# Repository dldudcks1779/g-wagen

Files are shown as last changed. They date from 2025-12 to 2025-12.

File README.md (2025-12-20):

# 떡상한 구독자 수! 바로 G바겐 뽑았습니다
<div align="center">
  <a href="https://www.youtube.com/watch?v=YYdsRcfBJVY">
    YouTube
  </a>
</div>

---

## 1. System Architecture
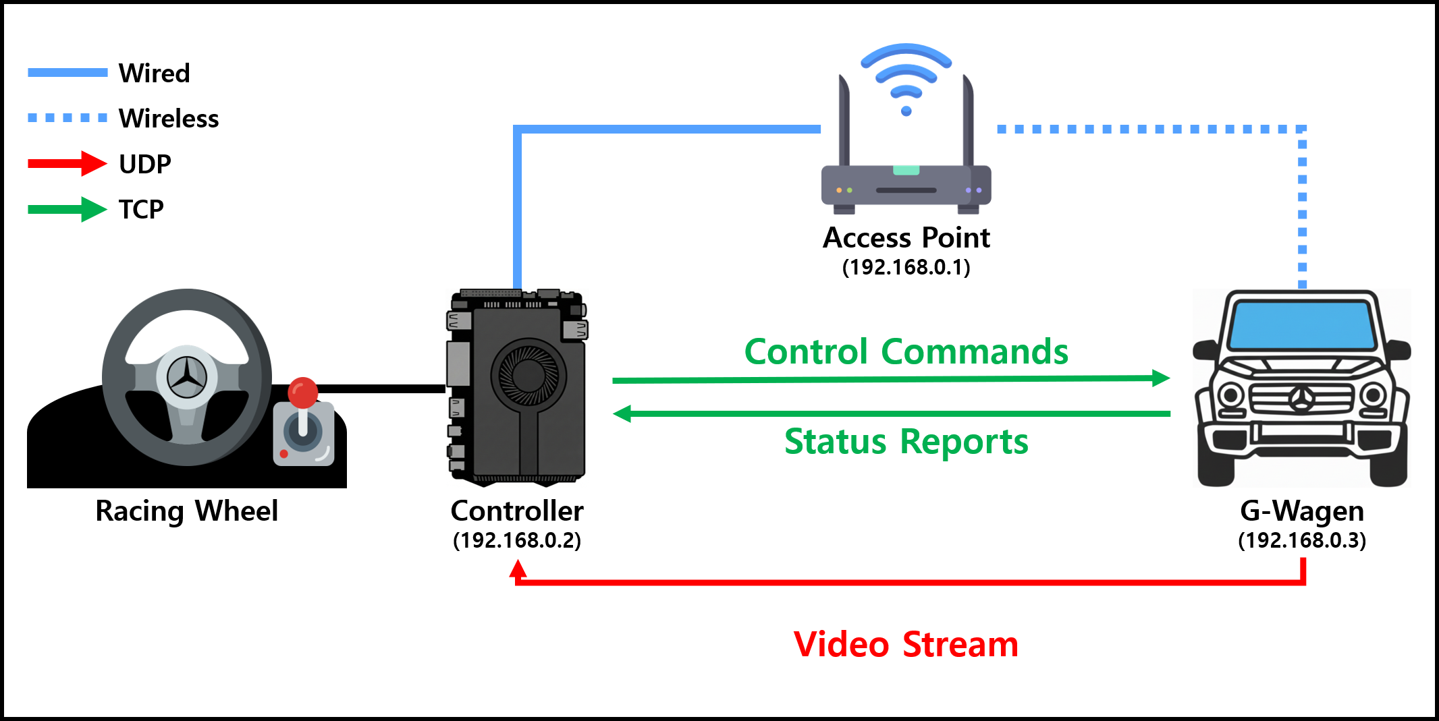
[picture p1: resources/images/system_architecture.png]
System Architecture


- **Video Stream**
    - **Protocol:** UDP
        - **Port:** 5000
    - **Codec:** MJPEG
    - **Resolution:** 1920x1080
    - **Frame Rate:** 15 fps
    - **Format:** Inline
- **Control Commands**
    - **Protocol:** TCP
        - **Port:** 5001
    - **Payload:** Steering Value, Steering Direction, Acceleration Percent, Brake Percent, Gear, Headlight, Hazard Light, Horn
- **Status Reports**
    - **Protocol:** TCP
        - **Port:** 5001
    - **Payload:** Battery SoC (State of Charge)
- **Access Point** 
    - **SSID (Service Set ID):** `Mercedes-Benz`
    - **PSK (Pre-Shared Key):** `20220608`

---

## 2. Hardware Information
### 2.1) G-Wagen
- **Main Board:** Raspberry Pi Zero 2 W
    - **Processor:** Broadcom BCM2710A1, quad-core 64-bit SoC (Arm Cortex-A53 @ 1GHz)
    - **Memory:** 512MB LPDDR2
    - **Storage:** 16GB microSD Card
    - **[Product Brief](./resources/[Raspberry%20Pi%20Zero%202%20W]%20Product%20Brief.pdf)**
- **Camera:** Raspberry Pi Camera Module V2 (8MP)
- **Motor Driver:** L9110S Dual H-Bridge
- **Speaker:** LM386 Audio Amplifier
- **Battery**
    - **Capacity:** 5000mAh (3.7V)
    - **Fuel Gauge:** Gravity 3.7V Li Battery Fuel Gauge SKU DFR0563
        - **Link:** [https://wiki.dfrobot.com/gravity__3.7v_li_battery_fuel_gauge_sku__dfr0563](https://wiki.dfrobot.com/gravity__3.7v_li_battery_fuel_gauge_sku__dfr0563)
    - **Management IC:** IP5306 (Li-ion Charge/Boost Controller)
- **Circuit Diagram**<br>
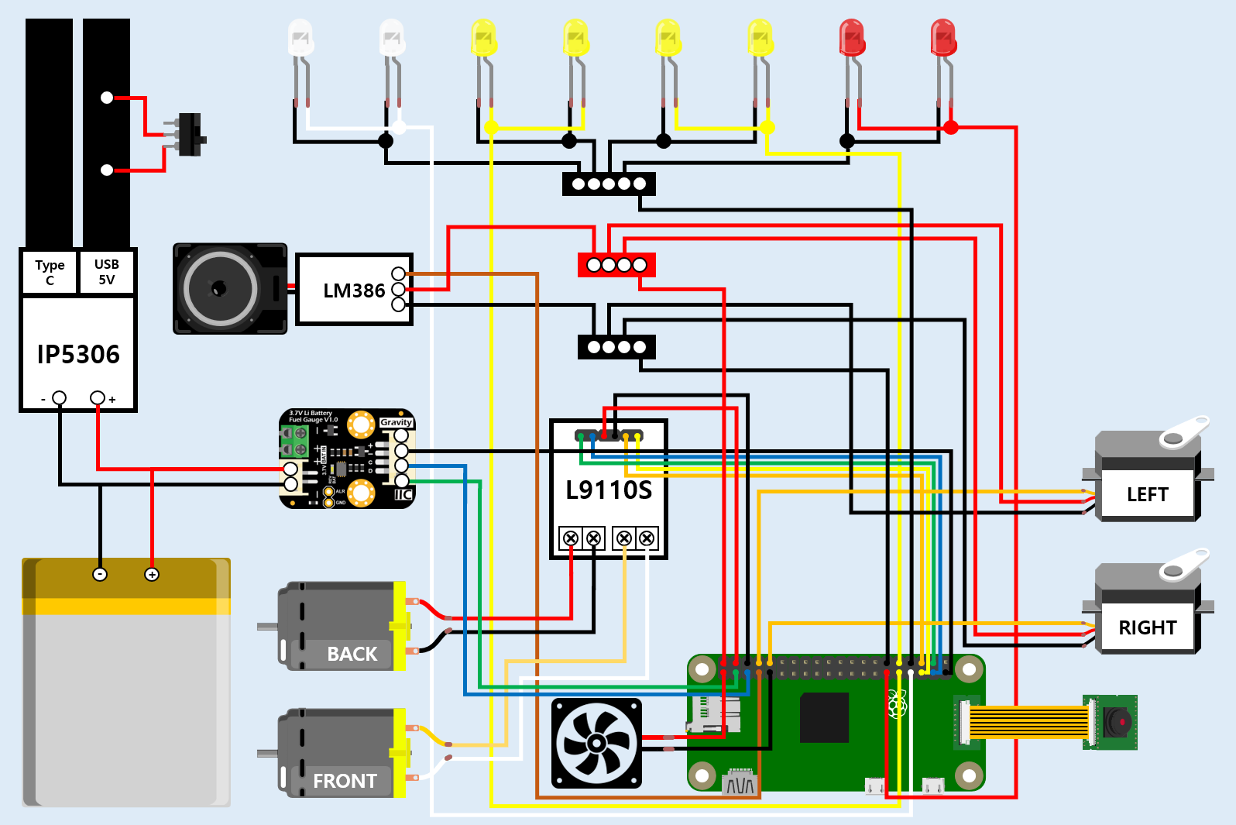
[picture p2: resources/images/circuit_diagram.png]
Circuit Diagram
    
### 2.2) Controller
- **Main Board:** LattePanda Sigma
    - **Processor:** Intel Core i5-1340P 12 Cores, 16 Threads Up to 4.6GHz
    - **Graphics:** Intel Iris Xe Graphics 80 Execution Units Up to 1.45GHz
    - **Memory:** 16GB Dual Channels LPDDR5 6400MHz
    - **Storage:** 512GB NVMe SSD
    - **Specification:** [https://docs.lattepanda.com/content/sigma_edition/Specification/](https://docs.lattepanda.com/content/sigma_edition/Specification/)
- **Racing Wheel:** [POWER RACER 270R REVOLUTION](./resources/[POWER%20RACER%20270R%20REVOLUTION]%20manual.pdf)

---

## 3. Software Information
### 3.1) G-Wagen
- **Operating System:** Raspberry Pi OS with Desktop (64-bit)
    - **Debian Codename:** Bookworm (Version 12)
    - **Download Link:** [https://downloads.raspberrypi.org/raspios_arm64/images/raspios_arm64-2025-05-13/](https://downloads.raspberrypi.org/raspios_arm64/images/raspios_arm64-2025-05-13/)
- **Language & Libraries**
    - 
        - 
- **Account Information**
    - **username:** `gwagen`
    - **password:** `0608`
### 3.2) Controller
- **Operating System:** Ubuntu with Desktop (64-bit)
    - **Debian Codename:** Noble Numbat (Version 24.04.3 LTS)
    - **Download Link:** [https://releases.ubuntu.com/noble/](https://releases.ubuntu.com/noble/)
- **Language & Libraries**
    - 
        -  
- **Account Information**
    - **username:** `controller`
    - **password:** `0608`

---

## 4. Setup Instructions
### 4.1) G-Wagen
#### 4.1.1) Raspberry Pi Configuration
- **Interfaces**    
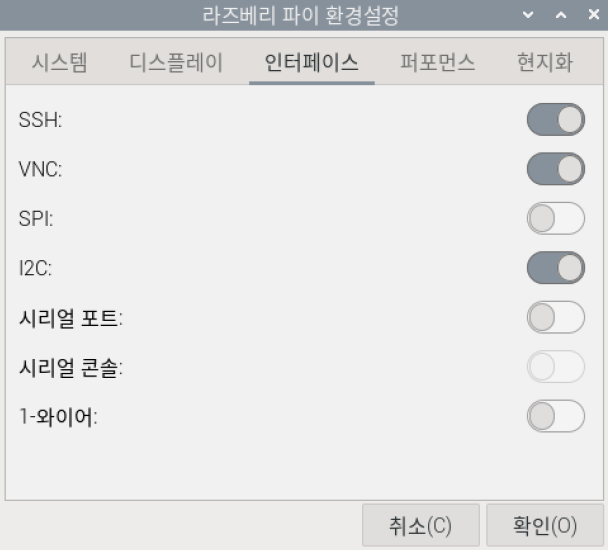
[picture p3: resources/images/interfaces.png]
    
    - **SSH (Secure Shell) Enabled**
    - **VNC (Virtual Network Computing) Enabled**
    - **I2C (Inter-Integrated Circuit) Enabled**
#### 4.1.2) System Update
- **Update Package List**
    ```bash
    sudo apt update
    ```
- **Upgrade Installed Packages**
    ```bash
    sudo apt upgrade -y
    ```
#### 4.1.3) Install Libraries
##### 4.1.3.1) System Dependencies and Core Packages (APT)
- **Install Required Packages**
    ```bash
    sudo apt install -y pigpio
    ```
    - **pigpio:** C library for Raspberry Pi which allows control of the General Purpose Input Outputs (GPIO)
##### 4.1.3.2) Specific Python Modules (pip3)
- **Install Required Python Modules**
    ```bash
    sudo pip3 install smbus2==0.5.0 --break-system-packages
    ```
    - **smbus2:** Pure Python implementation for I2C protocol communication
        - `--break-system-packages`: Allows installation of packages that may conflict with system packages
#### 4.1.4) Enable pigpio Daemon
- **Enable and Start pigpiod Service**
    ```bash
    sudo systemctl enable --now pigpiod
    ```
    - **systemctl:** Command to examine and control the systemd system and service manager
        - `--now`: Start the service immediately
### 4.2) Controller
#### 4.2.1) System Update
- **Update Package List**
    ```bash
    sudo apt update
    ```
- **Upgrade Installed Packages**
    ```bash
    sudo apt upgrade -y
    ```
#### 4.2.2) Install Libraries
##### 4.2.2.1) System Dependencies and Core Packages (APT)
- **Install Required Packages**
    ```bash
    sudo apt install -y python3-pip python3-opencv python3-pygame
    ```
    - **python3-pip:** Package installer for Python 3
    - **python3-opencv:** Library of programming functions primarily for real-time computer vision tasks
    - **python3-pygame:** Set of Python modules designed for writing video games
##### 4.2.2.2) Specific Python Modules (pip3)
- **Install Required Python Modules**
    ```bash
    sudo pip3 install pyinstaller --break-system-packages
    ```
    - **pyinstaller:** Tool to bundle Python applications into standalone executables
        - `--break-system-packages`: Allows installation of packages that may conflict with system packages

---

## 5. Start Video Stream on G-Wagen
- **Run rpicam-vid Command**
    ```bash
    rpicam-vid -t 0 --width 1920 --height 1080 --framerate 15 --codec mjpeg --inline --nopreview -o udp://192.168.0.2:5000
    ```
    - **rpicam-vid:** Command-line tool for streaming video from the Raspberry Pi Camera Module
        - `-t:` Duration of the video stream
        - `--width:` Width of the video frame
        - `--height:` Height of the video frame
        - `--framerate:` Frames per second
        - `--codec:` Video codec to use
        - `--inline:` Embed JPEG frames directly in the stream
        - `--nopreview:` Disable preview window
        - `-o:` Output destination

---

## 6. Auto-start G-Wagen Services on Boot
### 6.1) Create RPi Camera Video Stream Service
- **Open the file using a text editor**
    ```bash
    sudo vi /etc/systemd/system/rpicam.service
    ```
    - **Add the following content**
        ```ini
        [Unit]
        Description=RPi Camera Video Stream
        Wants=network-online.target
        After=network-online.target
        
        [Service]
        User=gwagen
        Group=gwagen
        Type=simple
        WorkingDirectory=/home/gwagen
        ExecStart=/usr/bin/rpicam-vid -t 0 --width 1920 --height 1080 --framerate 15 --codec mjpeg --inline --nopreview -o udp://192.168.0.2:5000
        Restart=on-failure
        RestartSec=5

        [Install]
        WantedBy=multi-user.target
        ```
        - **[Unit] Section**
            - `Description`: Brief description of the service
            - `Wants`: Specifies the target that this service wants to be started with
            - `After`: Specifies the order in which units are started
        - **[Service] Section**
            - `User`: User to run the service as
            - `Group`: Group to run the service as
            - `Type`: Specifies the process start-up type
            - `WorkingDirectory`: Directory where the service will run
            - `ExecStart`: Command to start the service
            - `Restart`: Defines the restart behavior on failure
            - `RestartSec`: Delay before restarting the service
        - **[Install] Section**
            - `WantedBy`: Specifies the target that this service should be started under
### 6.2) Create G-Wagen Application Service
- **Open the file using a text editor**
    ```bash
    sudo vi /etc/systemd/system/gwagen.service
    ```
    - **Add the following content**
        ```ini
        [Unit]
        Description=G-Wagen Application
        Wants=network-online.target
        After=network-online.target
        After=rpicam.service
        
        [Service]
        User=gwagen
        Group=gwagen
        Type=simple
        WorkingDirectory=/home/gwagen
        ExecStart=/usr/bin/python3 /home/gwagen/main.py
        Restart=on-failure
        RestartSec=5

        [Install]
        WantedBy=multi-user.target
        ```
        - **[Unit] Section**
            - `Description`: Brief description of the service
            - `Wants`: Specifies the target that this service wants to be started with
            - `After`: Specifies the order in which units are started
        - **[Service] Section**
            - `User`: User to run the service as
            - `Group`: Group to run the service as
            - `Type`: Specifies the process start-up type
            - `WorkingDirectory`: Directory where the service will run
            - `ExecStart`: Command to start the service
            - `Restart`: Defines the restart behavior on failure
            - `RestartSec`: Delay before restarting the service
        - **[Install] Section**
            - `WantedBy`: Specifies the target that this service should be started under
### 6.3) Enable Both Services
- **Reload Systemd Daemon**
    ```bash
    sudo systemctl daemon-reload
    ```
- **Enable both services to start on boot**
    ```bash
    sudo systemctl enable rpicam.service gwagen.service
    ```
- **Start both services immediately**
    ```bash
    sudo systemctl start rpicam.service gwagen.service
    ```
- **Check the status of both services**
    ```bash
    sudo systemctl status rpicam.service gwagen.service
    ```
### 6.4) Apply Changes
- **Apply Changes by Rebooting**
    ```bash
    sudo reboot
    ```

---

## 7. Build Controller Application Executable
- **Use PyInstaller to Create Executable**
    ```bash
    pyinstaller --onedir --noconsole --name controller main.py
    ```
    - **pyinstaller:** Tool to bundle Python applications into standalone executables
        - `--onedir:` Create a directory with the executable and dependencies
        - `--noconsole:` Do not provide a console window for standard i/o
        - `--name:` Specify the name of the executable file

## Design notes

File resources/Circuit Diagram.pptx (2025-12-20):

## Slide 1

Type
C

USB 5V

LM386

IP5306

+

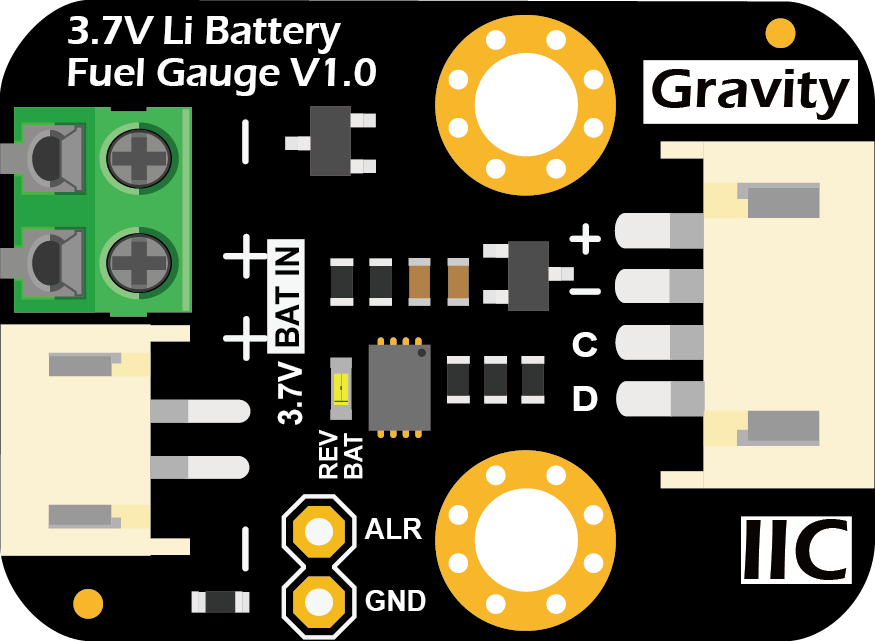
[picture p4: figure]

L9110S

LEFT

RIGHT

+

BACK

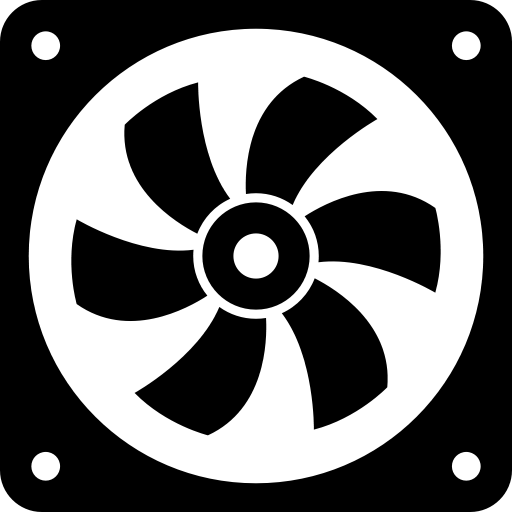
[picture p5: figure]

FRONT

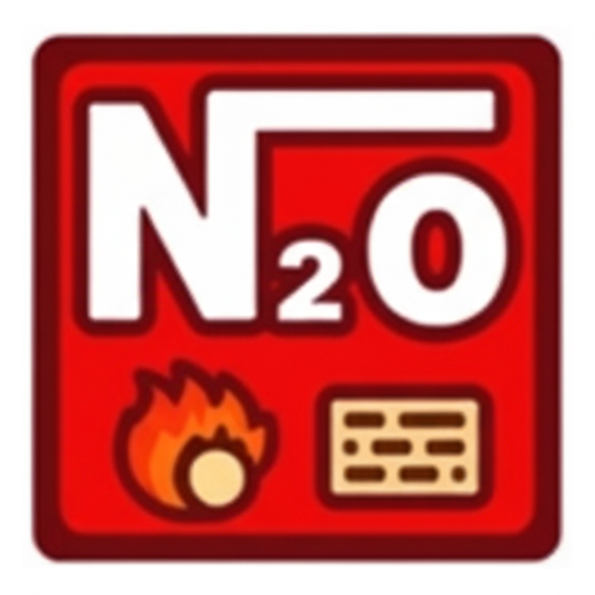
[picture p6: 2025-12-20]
controller/images/battery.png

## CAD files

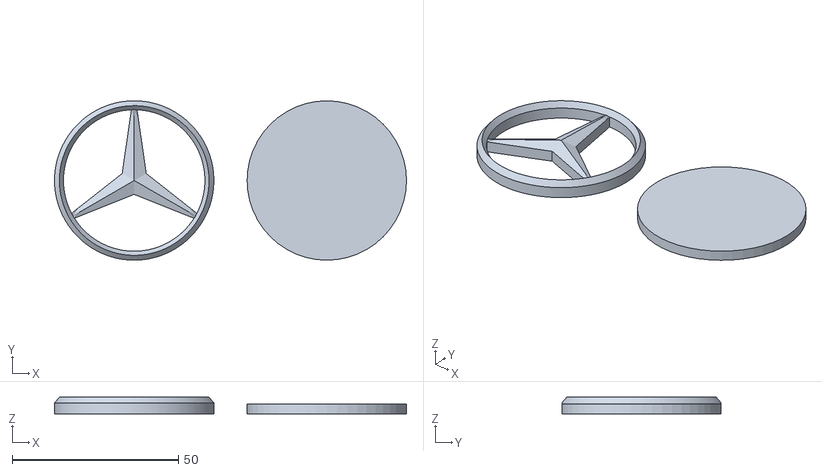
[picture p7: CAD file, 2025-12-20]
resources/3d/mercedes_benz_logo.stl
106.0 x 48.0 x 5.00

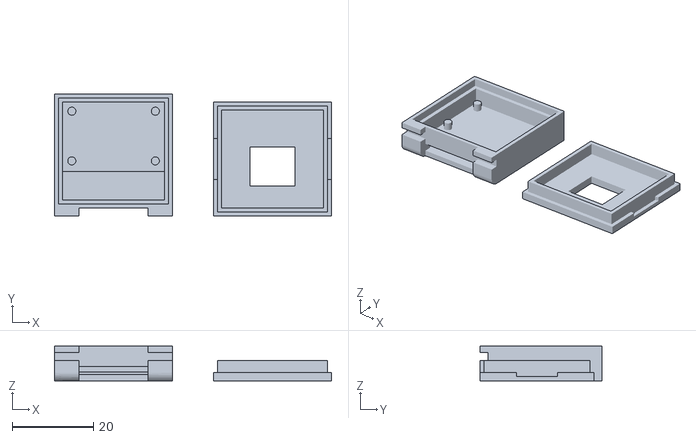
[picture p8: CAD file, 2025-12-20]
resources/3d/raspberry_pi_camera_case.stl
68.0 x 30.0 x 8.50

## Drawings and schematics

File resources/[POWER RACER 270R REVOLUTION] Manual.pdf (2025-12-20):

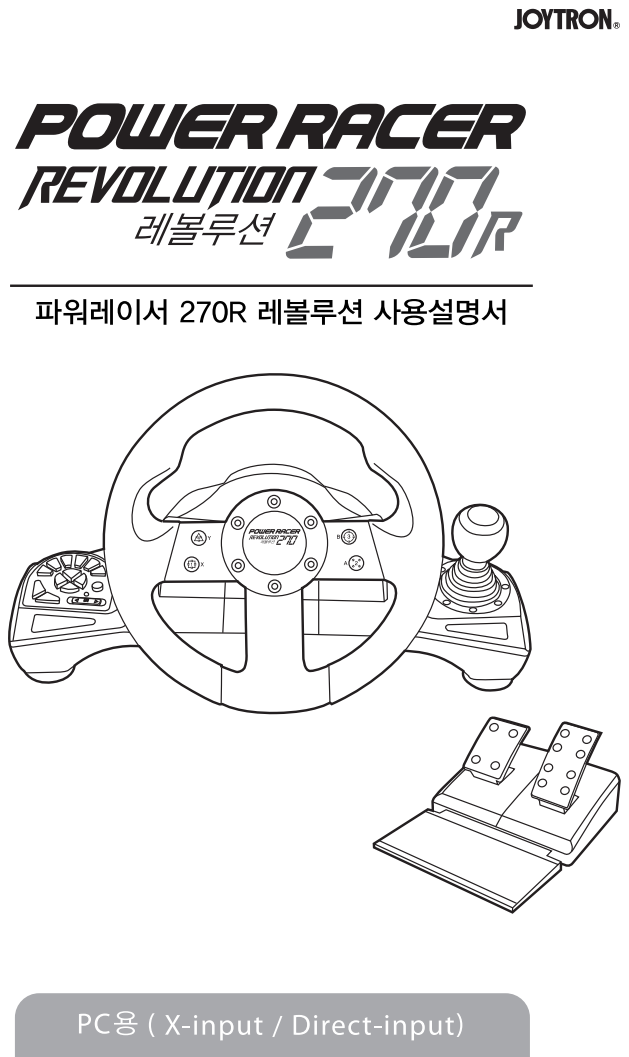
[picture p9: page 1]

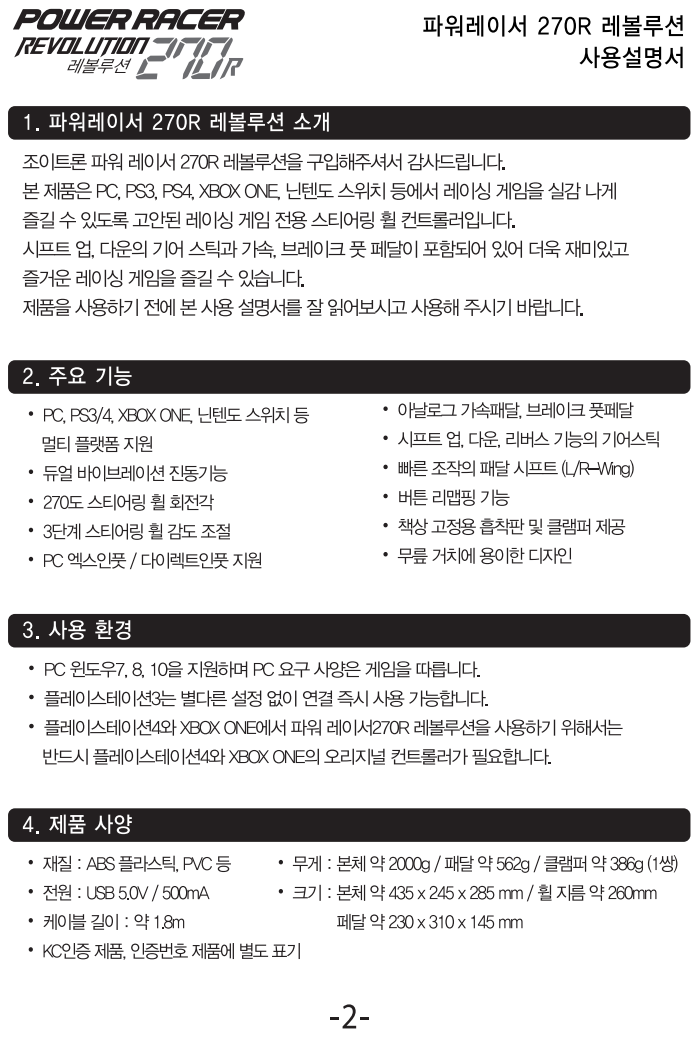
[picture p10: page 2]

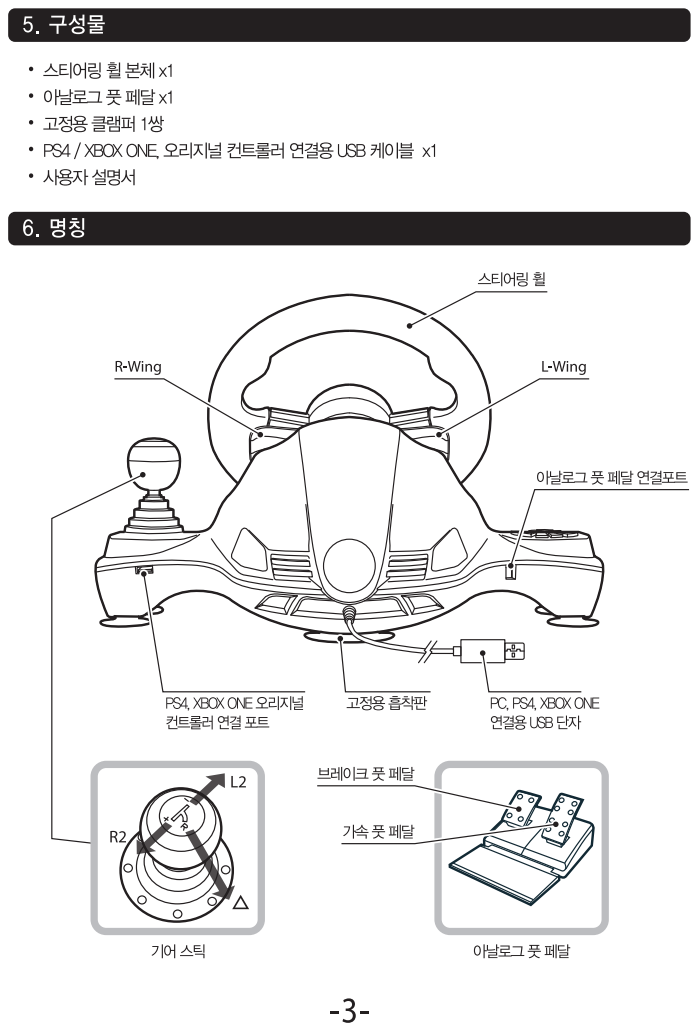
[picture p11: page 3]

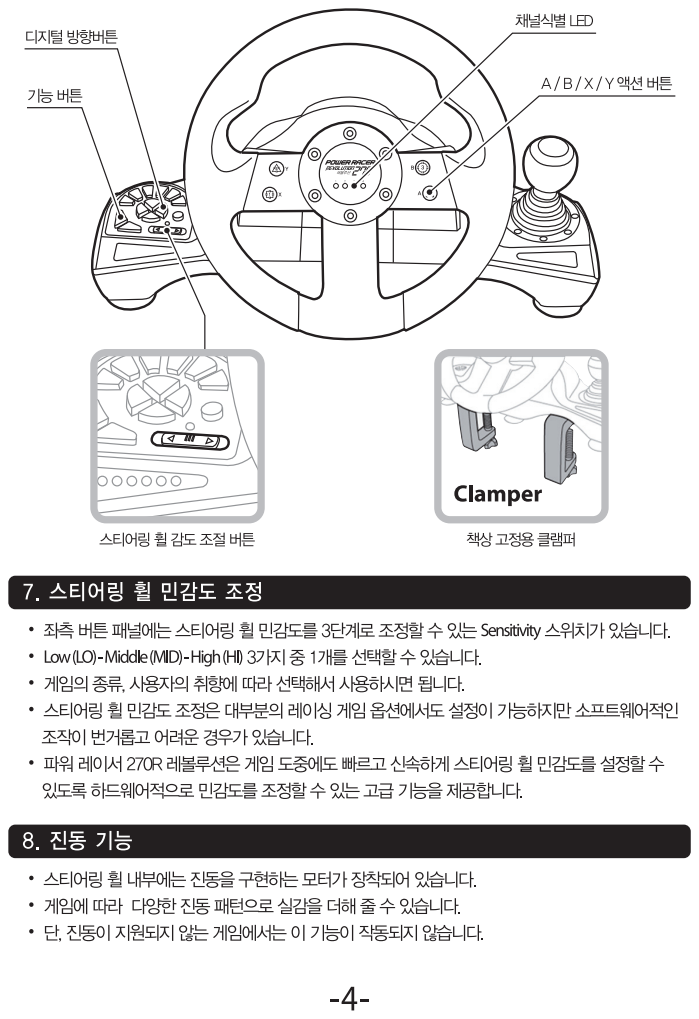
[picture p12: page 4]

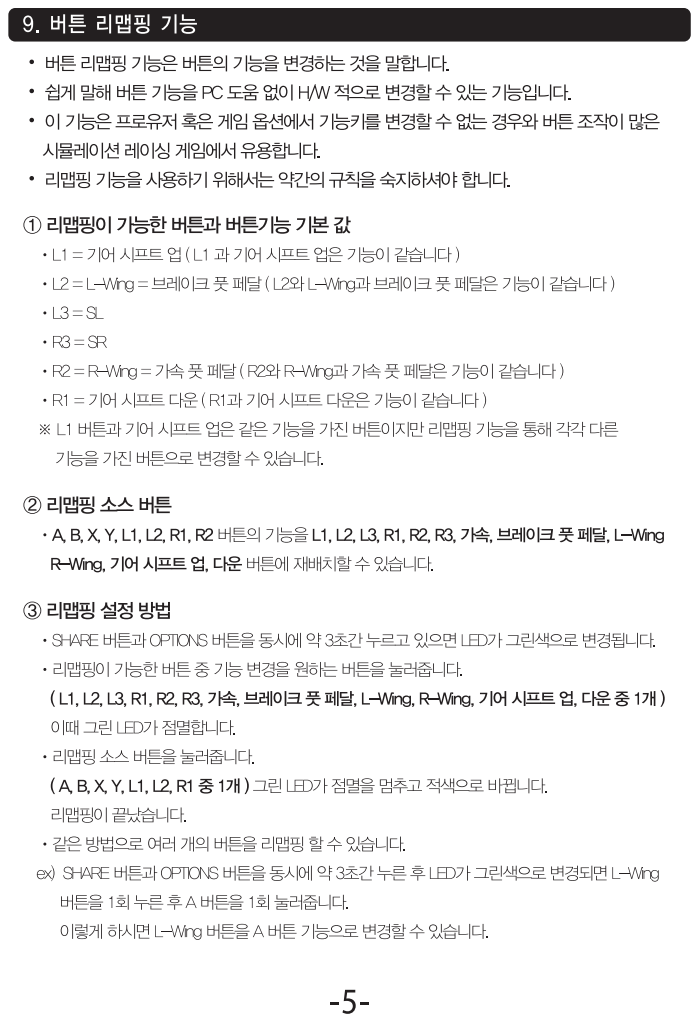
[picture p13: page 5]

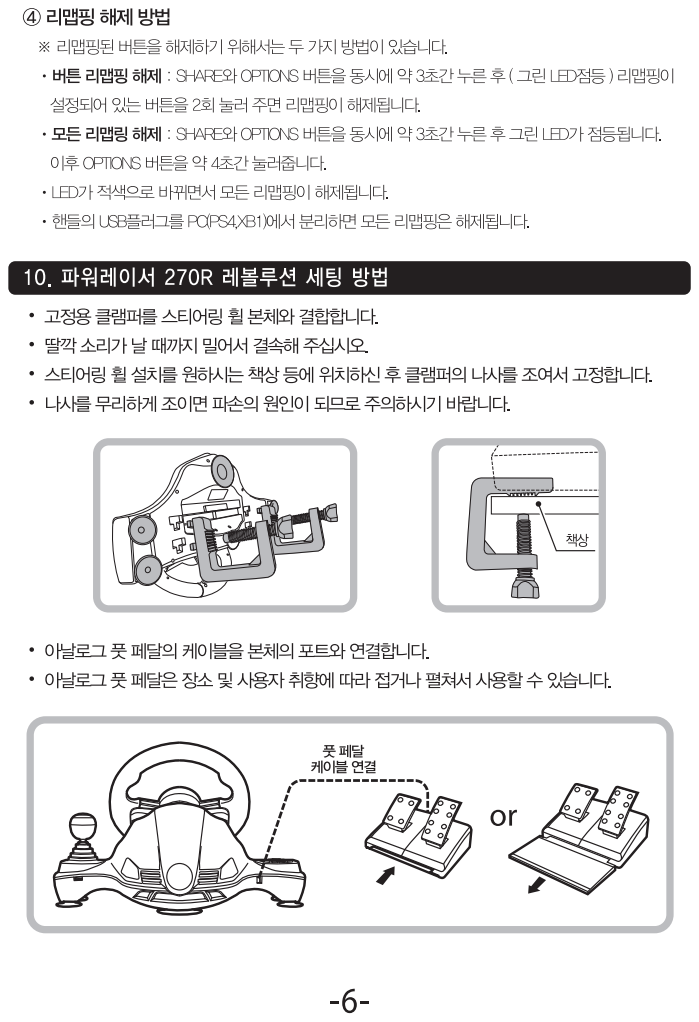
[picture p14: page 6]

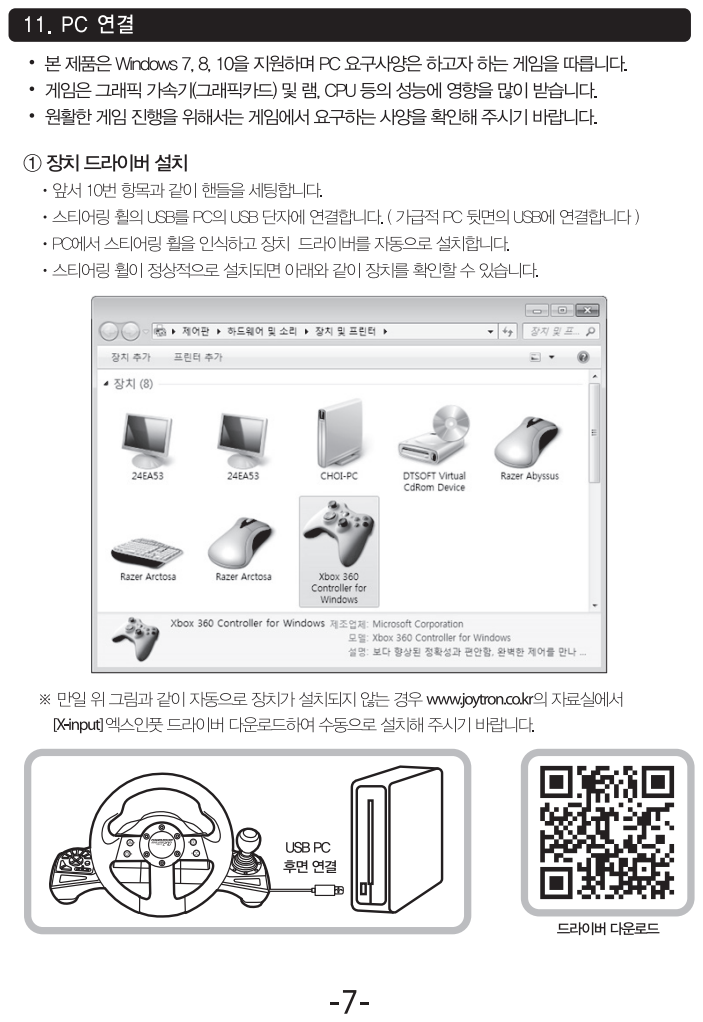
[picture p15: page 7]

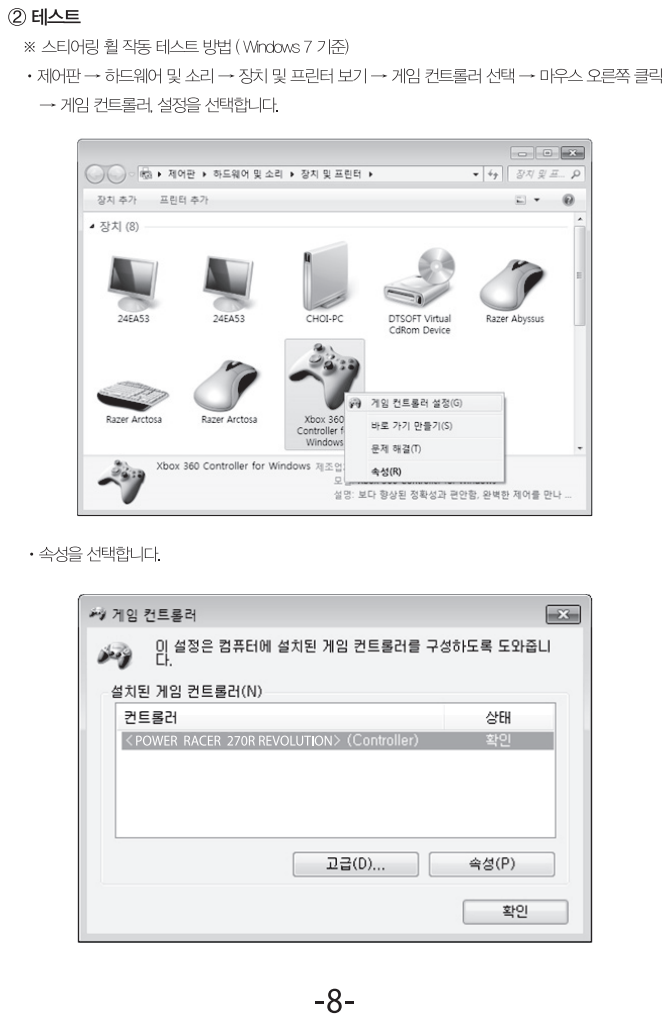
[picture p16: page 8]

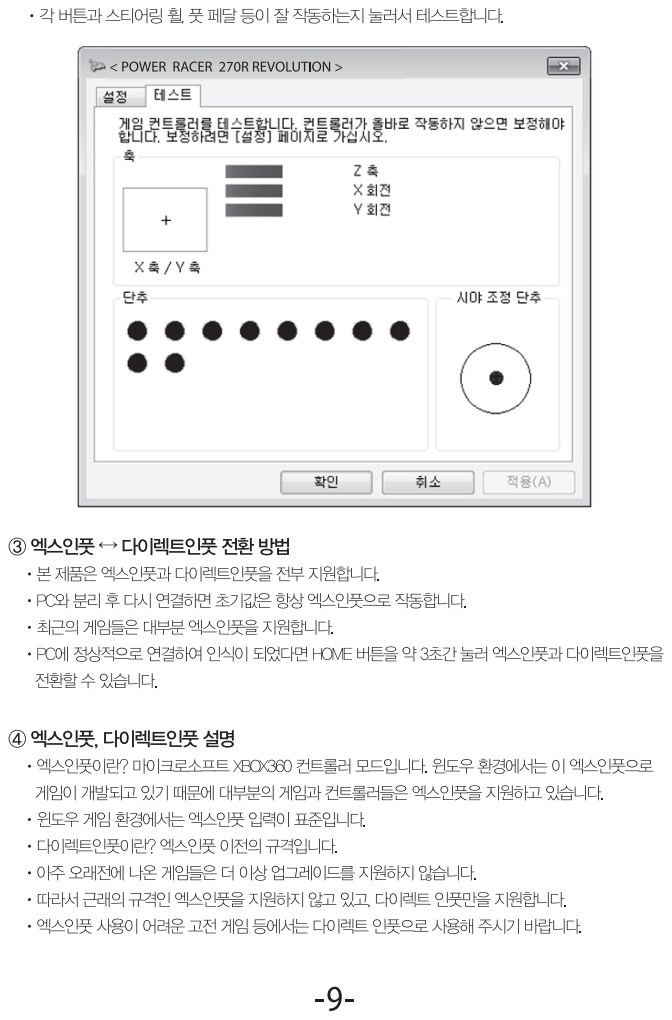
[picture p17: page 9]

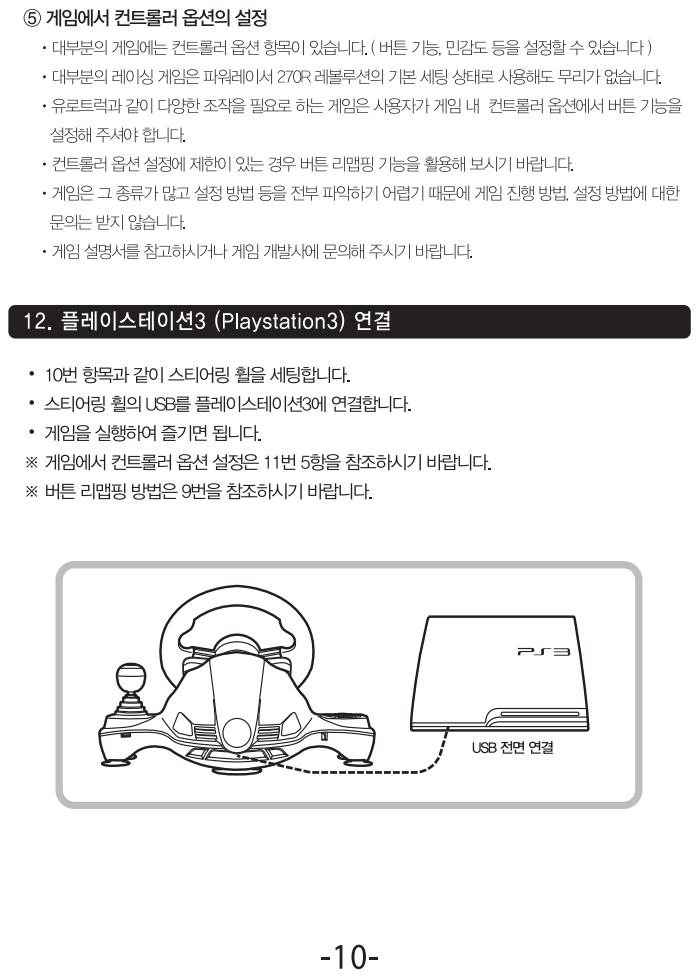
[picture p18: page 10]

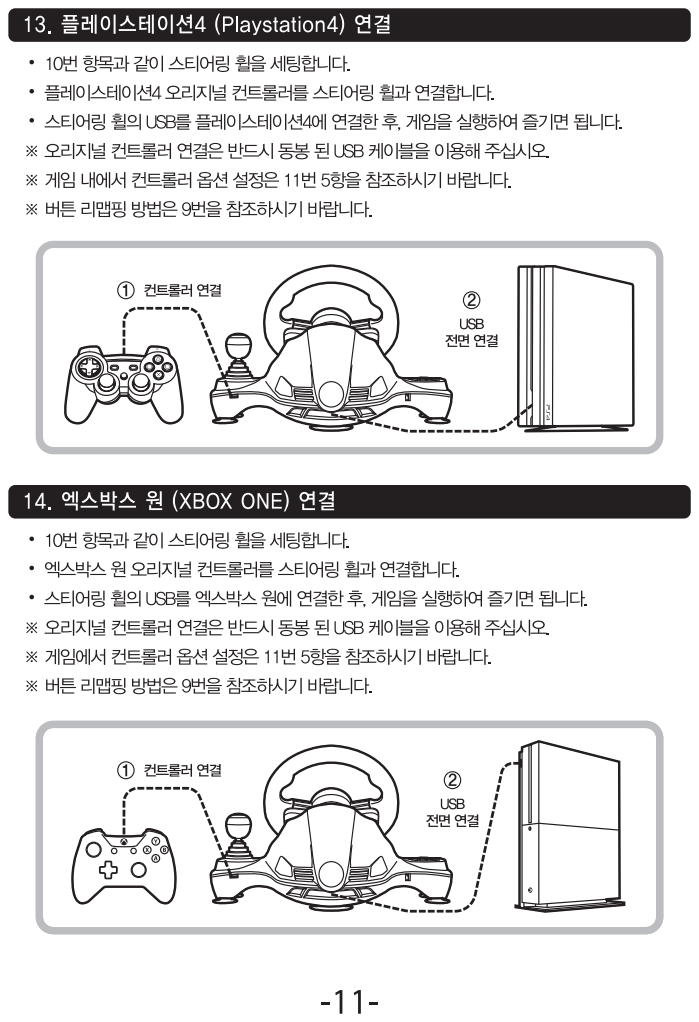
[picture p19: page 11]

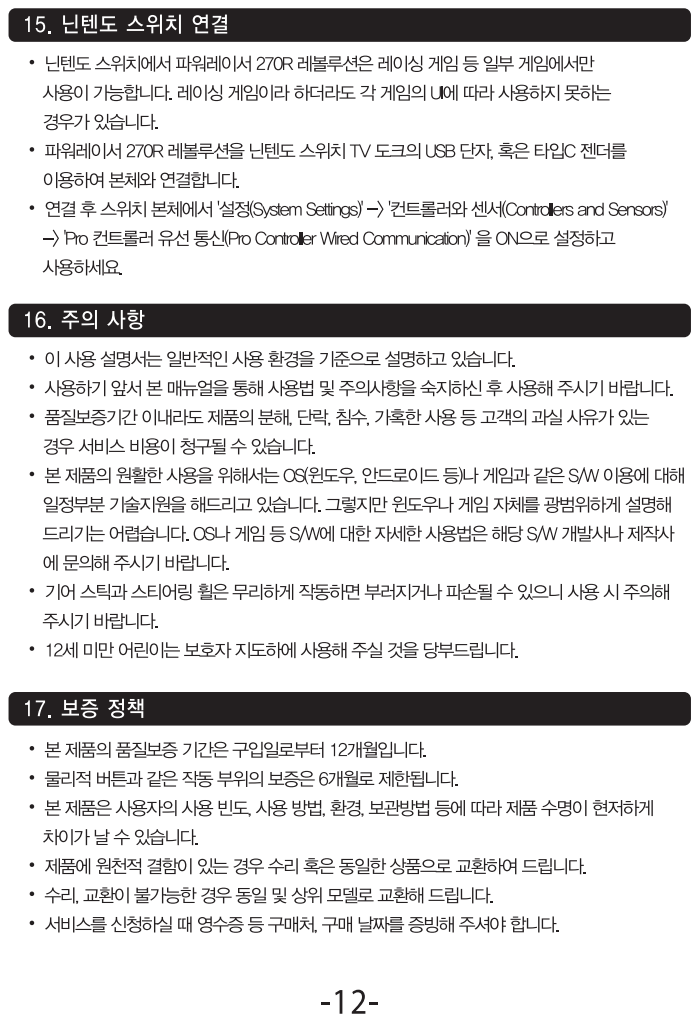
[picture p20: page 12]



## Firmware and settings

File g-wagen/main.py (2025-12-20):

import asyncio
import functools
import json
import signal
import RPi.GPIO as GPIO
import config
import led
import dc_motor
import servo_motor
import speaker
import battery

# 상태 딕셔너리
state = {}

# 현재 연결된 TCP 클라이언트 목록
ACTIVE_WRITERS = set()

# 모듈 (LED, DC 모터, 서보 모터, 스피커) 설정
def setup_modules(state: dict):
    led.setup_leds(state)
    dc_motor.setup_dc_motors(state)
    servo_motor.setup_servo_motors(state)
    speaker.setup_speaker()

# 모듈 (LED, DC 모터, 서보 모터, 스피커) 제어
async def control_modules(command: dict, state: dict):
    led.control_leds(command, state)
    dc_motor.control_dc_motors(command, state)
    servo_motor.control_servo_motors(command, state)
    speaker.honk(bool(command.get("horn", False)))

# 모듈 (LED, DC 모터, 서보 모터, 스피커) 정리
def cleanup_modules():
    try:
        led.cleanup_leds()
        dc_motor.cleanup_dc_motors()
        servo_motor.cleanup_servo_motors()
        speaker.cleanup_speaker()
    except Exception as exception:
        print(f"ERROR: 모듈 정리 실패 - {exception}")

# 리소스 (I2C, GPIO) 정리
def cleanup_resources(smbus=None):
    if smbus:
        try:
            smbus.close()
        except Exception as exception:
            print(f"ERROR: SMBus 종료 실패 - {exception}")
    try:
        GPIO.cleanup()
    except Exception as exception:
        print(f"ERROR: GPIO 정리 실패 - {exception}")

# SIGTERM 신호 처리기
def handle_sigterm(signum, frame):
    raise KeyboardInterrupt()

# SIGTERM 신호 처리 등록
signal.signal(signal.SIGTERM, handle_sigterm)

# TCP 연결 처리 비동기 루프
async def handle_connection_loop(stream_reader: asyncio.StreamReader, stream_writer: asyncio.StreamWriter, state: dict):
    peername = stream_writer.get_extra_info("peername")
    print(f"클라이언트 접속: {peername}")
    ACTIVE_WRITERS.add(stream_writer)
    try:
        while True:
            line = await stream_reader.readline()
            if not line:
                break
            try:
                command = json.loads(line.decode("utf-8").strip())
                await control_modules(command, state)
            except json.JSONDecodeError as error:
                print(f"ERROR: JSON 파싱 실패 - {error} (내용: {line.strip()})")
            except Exception as error:
                print(f"ERROR: 명령 처리 중 오류 - {error}")
    except (asyncio.CancelledError, ConnectionResetError):
        pass
    finally:
        print(f"클라이언트 연결 종료: {peername}")
        ACTIVE_WRITERS.discard(stream_writer)
        stream_writer.close()
        await stream_writer.wait_closed()

# 배터리 잔량 전송 비동기 루프
async def send_battery_soc_loop(smbus: battery.smbus2.SMBus):
    while True:
        try:
            soc = battery.get_battery_soc(smbus)
            print(f"배터리 잔량: {soc}%")
            message = json.dumps({"type": "battery", "soc": round(soc, 2)}).encode() + b"\n"
            ACTIVE_WRITERS.difference_update({w for w in ACTIVE_WRITERS if w.is_closing()})
            for stream_writer in list(ACTIVE_WRITERS):
                try:
                    stream_writer.write(message)
                    await stream_writer.drain()
                except (ConnectionResetError, BrokenPipeError):
                    ACTIVE_WRITERS.discard(stream_writer)
        except Exception as exception:
            print(f"ERROR: 배터리 잔량 전송 오류 - {exception}")
        await asyncio.sleep(config.BATTERY_CHECK_INTERVAL_SECONDS)

# 메인 비동기 함수
async def main(state: dict, smbus):
    client = functools.partial(handle_connection_loop, state=state)
    server = await asyncio.start_server(client, config.HOST, config.PORT)
    async with server:
        await asyncio.gather(
            server.serve_forever(),
            led.hazard_light_blink_loop(state),
            servo_motor.update_brake_loop(state),
            send_battery_soc_loop(smbus)
        )

if __name__ == "__main__":
    try:
        GPIO.setmode(GPIO.BCM)
        setup_modules(state)
        smbus = battery.init_smbus()        
        asyncio.run(main(state, smbus))
    except Exception as exception:
        print(exception)
    finally:
        print("프로그램 종료")
        cleanup_modules()
        cleanup_resources(smbus)

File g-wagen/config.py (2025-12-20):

# G-WAGEN TCP 서버 설정
HOST = "0.0.0.0" # 호스트 주소
PORT = 5001      # 포트 번호

# GPIO 핀 번호 (BCM)
HEADLIGHT_LED_PIN = 13         # 전조등 LED
HAZARD_LIGHT_FRONT_LED_PIN = 6 # 비상등 앞 LED
HAZARD_LIGHT_BACK_LED_PIN = 12 # 비상등 뒤 LED
BRAKE_LIGHT_LED_PIN = 5        # 브레이크등 LED
DRIVE_DC_MOTOR_PIN = 20        # 전진 DC 모터 
REVERSE_DC_MOTOR_PIN = 26      # 후진 DC 모터
LEFT_DC_MOTOR_PIN = 16         # 좌회전 DC 모터
RIGHT_DC_MOTOR_PIN = 19        # 우회전 DC 모터
LEFT_SERVO_MOTOR_PIN = 14      # 왼쪽 서보 모터
RIGHT_SERVO_MOTOR_PIN = 15     # 오른쪽 서보 모터
HONK_SPEAKER_PIN = 4           # 경적 스피커

# 서보 모터 설정
SERVO_MOTOR_MIN_ANGLE = 0.0               # 최소 각도
SERVO_MOTOR_MAX_ANGLE = 180.0             # 최대 각도
SERVO_MOTOR_PULSE_WIDTH_MIN = 500         # 펄스 폭 최솟값 (μs)
SERVO_MOTOR_PULSE_WIDTH_MAX = 2500        # 펄스 폭 최댓값 (μs)
SERVO_MOTOR_LEFT_BASE_ANGLE = 85          # 왼쪽 기준 각도
SERVO_MOTOR_RIGHT_BASE_ANGLE = 30         # 오른쪽 기준 각도
SERVO_MOTOR_MAX_TRAVEL_DEGREE = 10.0      # 최대 이동 각도
SERVO_MOTOR_DEADBAND_PERCENT = 1.0        # 입력 신호 무시 구간 (%)
SERVO_MOTOR_DEADBAND_DEGREE = 1.0         # 목표 각도 도달 시 허용 오차 (°)
SERVO_MOTOR_FREQUENCY = 50                # 주파수 (Hz)
SERVO_MOTOR_MAX_DEGREE_PER_SECOND = 180.0 # 최대 회전 속도 (°/s)

# I2C 통신 설정 (MAX17043 배터리 잔량 측정 IC)
MAX17043_I2C_ADDRESS = 0x36  # MAX17043 칩의 I2C 장치 주소
MAX17043_SOC_REGISTER = 0x04 # 칩 내부의 배터리 잔량(SoC) 값이 저장된 레지스터 주소

# 배터리 체크 주기 (초)
BATTERY_CHECK_INTERVAL_SECONDS = 5.0

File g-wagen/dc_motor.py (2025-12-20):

import RPi.GPIO as GPIO
import config

# DC 모터 PWM 객체
pwm_drive = None
pwm_reverse = None
pwm_left_steering = None
pwm_right_steering = None

# DC 모터 초기화
def setup_dc_motors(state: dict):
    global pwm_drive, pwm_reverse, pwm_left_steering, pwm_right_steering
    for pin in (config.DRIVE_DC_MOTOR_PIN, config.REVERSE_DC_MOTOR_PIN, config.LEFT_DC_MOTOR_PIN, config.RIGHT_DC_MOTOR_PIN):
        GPIO.setup(pin, GPIO.OUT, initial=GPIO.LOW)
    pwm_drive = GPIO.PWM(config.DRIVE_DC_MOTOR_PIN, 500)
    pwm_reverse = GPIO.PWM(config.REVERSE_DC_MOTOR_PIN, 500)
    pwm_left_steering = GPIO.PWM(config.LEFT_DC_MOTOR_PIN, 500)
    pwm_right_steering = GPIO.PWM(config.RIGHT_DC_MOTOR_PIN, 500)
    for pwm in (pwm_drive, pwm_reverse, pwm_left_steering, pwm_right_steering):
        pwm.start(0)
    state["gear"] = "N"

# 전진 (D)
def drive(accel_percent: float):
    pwm_reverse.ChangeDutyCycle(0)
    pwm_drive.ChangeDutyCycle(accel_percent)

# 후진 (R)
def reverse(accel_percent: float):
    pwm_drive.ChangeDutyCycle(0)
    pwm_reverse.ChangeDutyCycle(accel_percent)

# 중립 (N)
def neutral():
    pwm_drive.ChangeDutyCycle(0)
    pwm_reverse.ChangeDutyCycle(0)

# 기어 제어
def control_gear(gear: str, brake_percent: float, accel_percent: float, state: dict):
    if brake_percent > 50 and gear in ("D", "R", "N"):
        state["gear"] = gear
    current_gear = state.get("gear", "N")
    if current_gear == "D":
        drive(accel_percent)
    elif current_gear == "R":
        reverse(accel_percent)
    else:
        neutral()

# 좌회전
def left_steering(steering_percent: float):
    pwm_right_steering.ChangeDutyCycle(0)
    pwm_left_steering.ChangeDutyCycle(steering_percent)

# 우회전
def right_steering(steering_percent: float):
    pwm_left_steering.ChangeDutyCycle(0)
    pwm_right_steering.ChangeDutyCycle(steering_percent)

# 조향 중앙
def center_steering():
    pwm_left_steering.ChangeDutyCycle(0)
    pwm_right_steering.ChangeDutyCycle(0)

# 조향 제어
def control_steering(steering_value: float, steering_direction: str):
    if steering_direction == "LEFT":
        left_steering(abs(steering_value) * 100)
    elif steering_direction == "RIGHT":
        right_steering(abs(steering_value) * 100)
    else:
        center_steering()

# DC 모터 제어
def control_dc_motors(command: dict, state: dict):
    steering_value = command.get("steering_value", 0.0)
    steering_direction = command.get("steering_direction", "CENTER")
    gear = command.get("gear", "N")
    brake_percent = float(command.get("brake_percent", 0.0))
    accel_percent = float(command.get("accel_percent", 0.0))
    control_gear(gear, brake_percent, accel_percent, state)
    control_steering(steering_value, steering_direction)

# DC 모터 정리
def cleanup_dc_motors():
    for pwm in (pwm_drive, pwm_reverse, pwm_left_steering, pwm_right_steering):
        if pwm:
            pwm.stop()

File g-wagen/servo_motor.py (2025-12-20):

import pigpio
import asyncio
import math
import config

# 서보 모터 pigpio 객체
pi = None

# 펄스 폭 변환
def angle_to_pulse_width(angle: float):
    clamped_angle = max(config.SERVO_MOTOR_MIN_ANGLE, min(config.SERVO_MOTOR_MAX_ANGLE, angle))
    ratio = (clamped_angle - config.SERVO_MOTOR_MIN_ANGLE) / (config.SERVO_MOTOR_MAX_ANGLE - config.SERVO_MOTOR_MIN_ANGLE)
    return int(config.SERVO_MOTOR_PULSE_WIDTH_MIN + (config.SERVO_MOTOR_PULSE_WIDTH_MAX - config.SERVO_MOTOR_PULSE_WIDTH_MIN) * ratio)

# 서보 모터 초기화
def setup_servo_motors(state: dict):
    global pi
    pi = pigpio.pi()
    if not pi.connected:
        raise RuntimeError("ERROR: pigpio 데몬 연결 실패")
    state["brake"] = {
        "current_left": config.SERVO_MOTOR_LEFT_BASE_ANGLE,
        "current_right": config.SERVO_MOTOR_RIGHT_BASE_ANGLE,
        "target_left": config.SERVO_MOTOR_LEFT_BASE_ANGLE,
        "target_right": config.SERVO_MOTOR_RIGHT_BASE_ANGLE
    }
    pi.set_servo_pulsewidth(config.LEFT_SERVO_MOTOR_PIN, angle_to_pulse_width(state["brake"]["current_left"]))
    pi.set_servo_pulsewidth(config.RIGHT_SERVO_MOTOR_PIN, angle_to_pulse_width(state["brake"]["current_right"]))

# 서보 모터 제어
def control_servo_motors(command: dict, state: dict):
    brake_percent = float(command.get("brake_percent", 0.0))
    brake_percent = max(0.0, min(100.0, brake_percent)) if abs(brake_percent) >= config.SERVO_MOTOR_DEADBAND_PERCENT else 0.0
    delta = config.SERVO_MOTOR_DEADBAND_DEGREE * (brake_percent / 100.0)
    state["brake"]["target_left"] = max(0, min(180, config.SERVO_MOTOR_LEFT_BASE_ANGLE + max(0, min(config.SERVO_MOTOR_MAX_TRAVEL_DEGREE, delta)) * 10))
    state["brake"]["target_right"] = max(0, min(180, config.SERVO_MOTOR_RIGHT_BASE_ANGLE + max(-config.SERVO_MOTOR_MAX_TRAVEL_DEGREE, min(0, -delta)) * 10))

# 브레이크 업데이트
def update_brake(state_brake: dict, current: str, target: str, degree: float, pin: int):
    difference = state_brake[target] - state_brake[current]
    if abs(difference) > config.SERVO_MOTOR_DEADBAND_DEGREE:
        state_brake[current] += math.copysign(min(abs(difference), degree), difference)
        pi.set_servo_pulsewidth(pin, angle_to_pulse_width(state_brake[current]))

# 브레이크 업데이트 비동기 루프
async def update_brake_loop(state: dict):
    degree = config.SERVO_MOTOR_MAX_DEGREE_PER_SECOND / config.SERVO_MOTOR_FREQUENCY
    while True:
        update_brake(state["brake"], "current_left", "target_left", degree, config.LEFT_SERVO_MOTOR_PIN)
        update_brake(state["brake"], "current_right", "target_right", degree, config.RIGHT_SERVO_MOTOR_PIN)
        await asyncio.sleep(1.0 / config.SERVO_MOTOR_FREQUENCY)

# 서보 모터 정리
def cleanup_servo_motors():
    if pi and pi.connected:
        for pin in (config.LEFT_SERVO_MOTOR_PIN, config.RIGHT_SERVO_MOTOR_PIN):
            pi.set_servo_pulsewidth(pin, 0)
        pi.stop()
